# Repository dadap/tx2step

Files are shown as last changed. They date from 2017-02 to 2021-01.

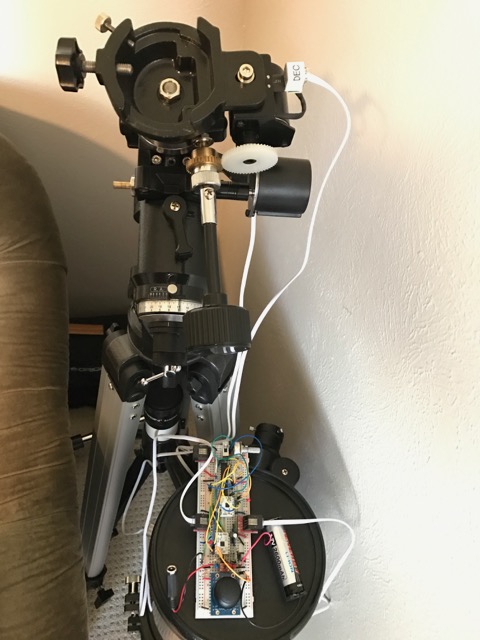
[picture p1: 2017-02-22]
img/tx2step-breadboard-proto.jpg

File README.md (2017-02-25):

Texas Two Step: A dual axis motor controller for equatorial telescope mounts
============================================================================

![Texas Two Step breadboard prototype controlling an unloaded Orion Astroview]
(https://github.com/dadap/tx2step/raw/master/img/tx2step-breadboard-proto.jpg)

Introduction
------------

The Texas Two Step is a replacement hand controller for the Synta Dual-Axis
motor kit for EQ-3 and EQ-5 type equatorial mounts (it can probably be adapted
to other mount designs utilizing stepper motors as well), with the following
improvements:

* Faster setting rates (original HC is limited to 8x sidereal)
* Analog 2-axis joystick to control setting rates (instead of rate slider switch
  combined with directional pad)
* ST-4 support with independent guiding (ST-4) and setting (joystick) rates.
* Main unit attaches to mount; RA, DEC, ST-4 cables move with telescope, and a
  single cable connects the control unit to a handheld joystick unit.
* Integrated rechargeable battery (to replace 4x D-cell pack, and eliminate the
  additional cable for power)
* All LEDs are dim and red to preserve dark adaptation
* Additional tracking rates (solar, lunar)
* Smaller and lighter
* Lower power draw (current prototype draws about .5 W for tracking)

The Texas Two Step is powered by an Atmel AVR microprocessor (currently an
Atmega328P on a breadboarded prototype circuit) and the stepper motors are
driven by dual TI DRV8834 low-voltage stepper driver ICs. The DRV8834 is
selected to allow a common power source (5V, boosted up from the output of a
single 18650 LiIon cell) for the logic and the motors.

TODO
----

A schematic and PCB layout should eventually be added to this repository.

The following features are not yet implemented:

* Directional switching not implemented; RA tracking direction is dependent on
  the order of stepper motor wiring to the driver boards. The final design is
  intended to allow switching between northern and southern hemisphere operation
  via a DIP switch or jumper setting.

The following features may or may not eventually be implemented:

* Backlash compensation (probably in the declination axis only; RA guiding at
  less than 1x tracking rate requires no backlash compensation.)
* Periodic error correction: implementing this will probably require some form
  of persistent storage, as the available EEPROM storage on the microcontroller
  is likely insufficient.

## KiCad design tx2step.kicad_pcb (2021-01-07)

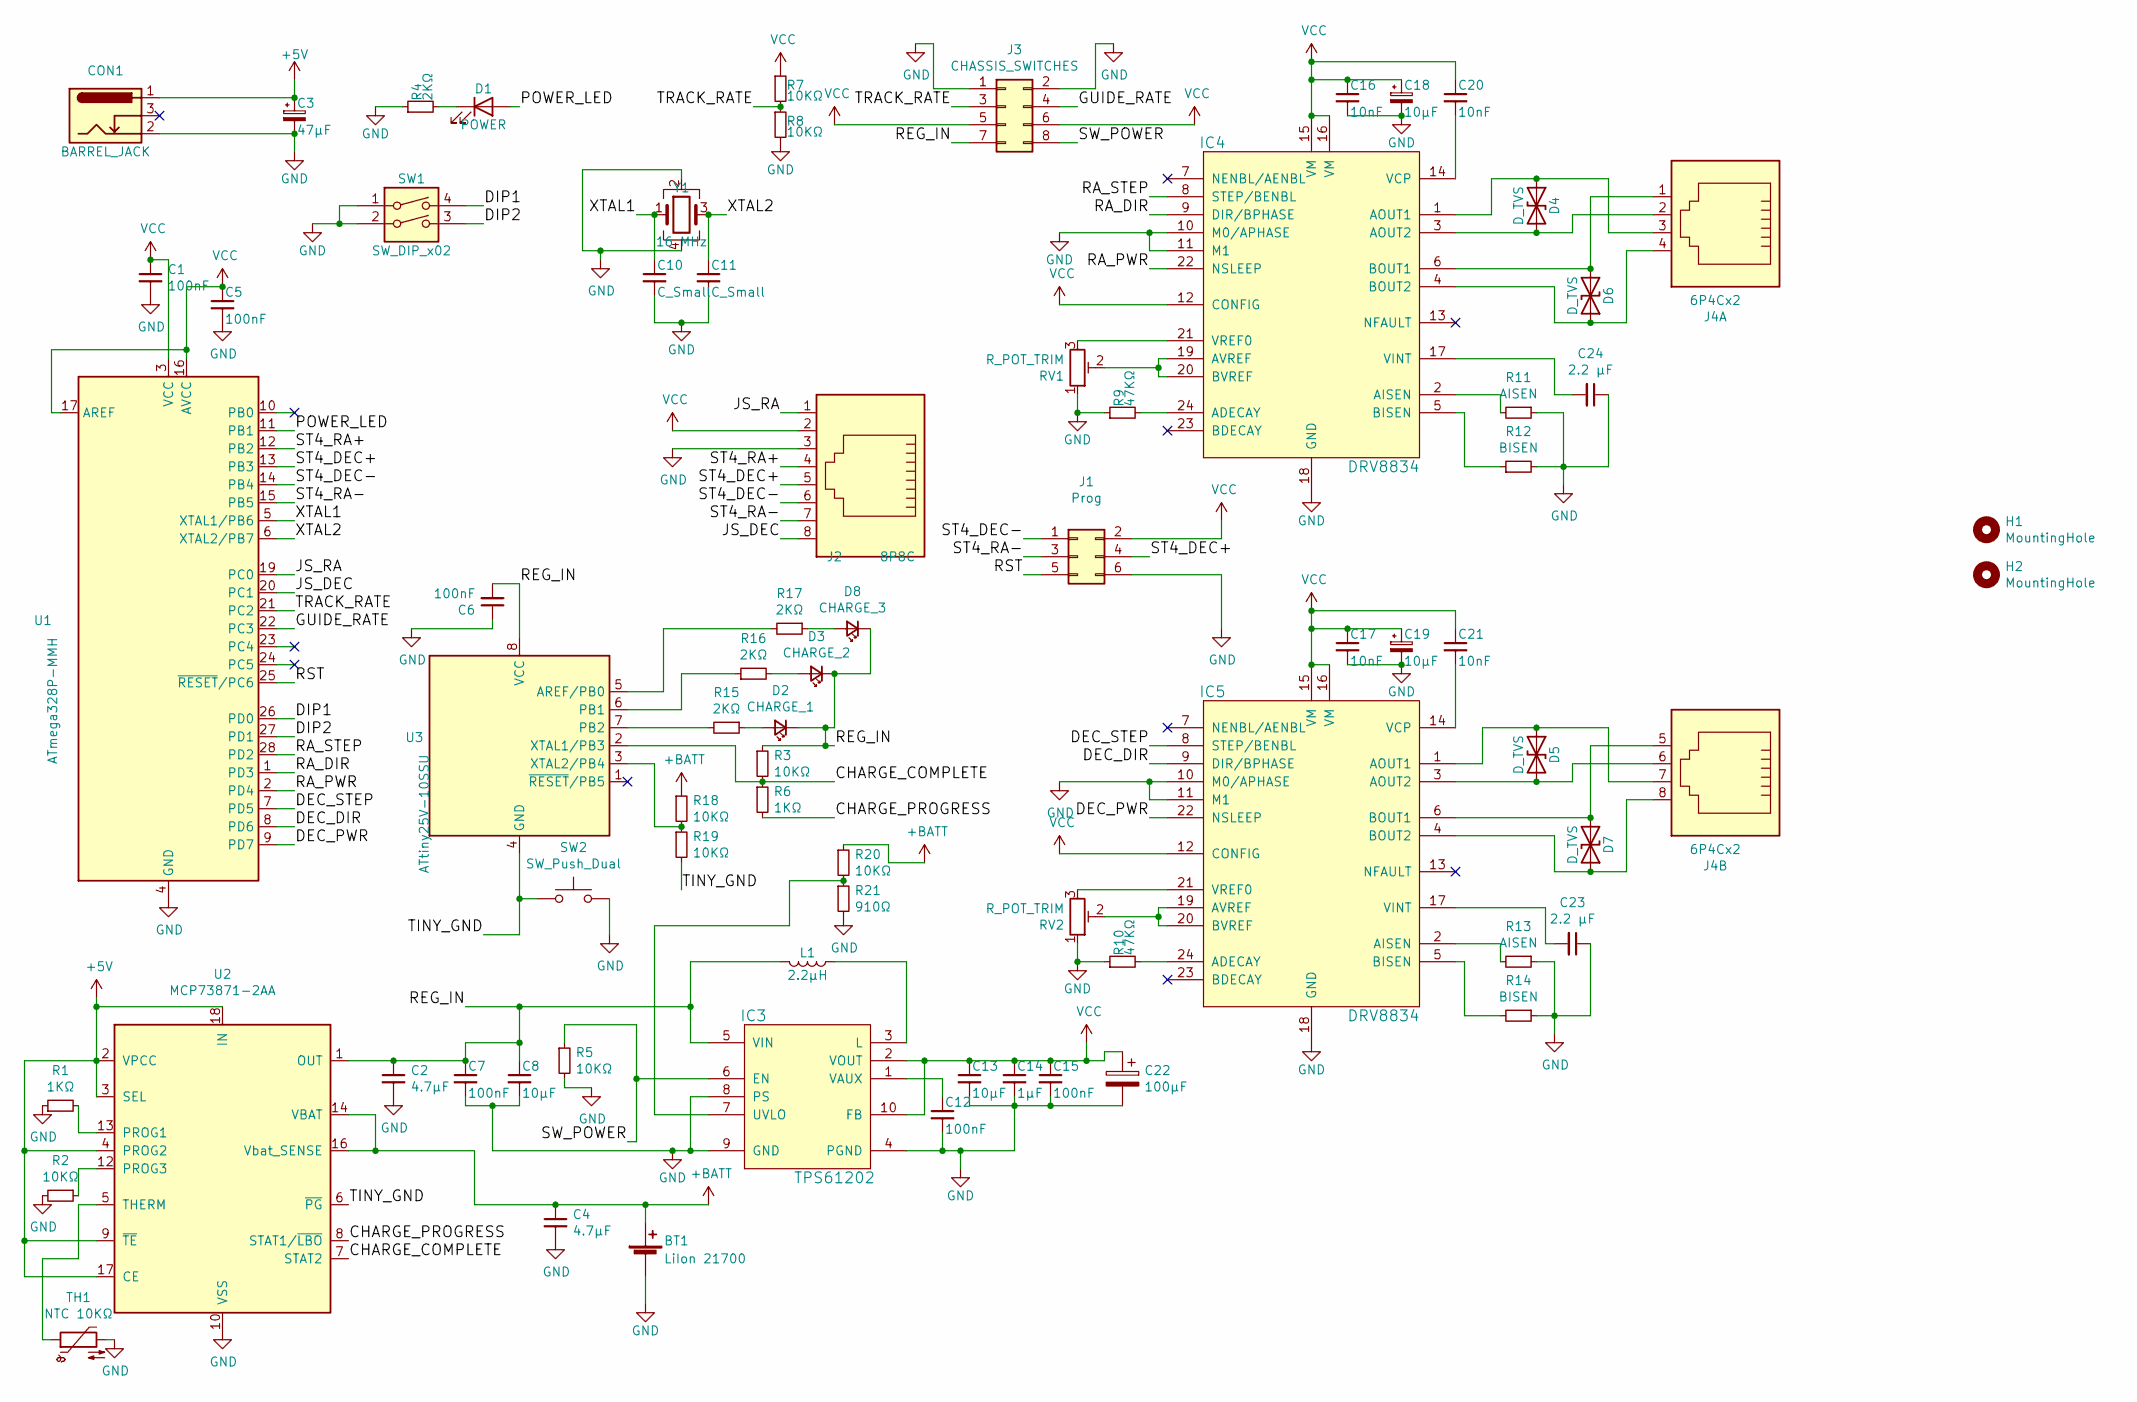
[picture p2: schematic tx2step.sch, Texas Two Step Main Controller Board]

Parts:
BT1: LiIon 21700; Battery_Clip_21700
C1, C5, C6, C7, C12, C15: 100nF; C_0603_1608Metric
C2, C4: 4.7µF; C_0603_1608Metric
C3: 47µF; CP_Radial_D5.0mm_P2.00mm
C8, C13, C18, C19: 10µF; C_0805_2012Metric
C10, C11: C_Small; C_0603_1608Metric
C14: 1µF; C_0603_1608Metric
C16, C17, C20, C21: 10nF; C_0603_1608Metric
C22: 100µF; CP_Radial_D5.0mm_P2.00mm
C23, C24: 2.2 µF; C_0603_1608Metric
CON1: BARREL_JACK; BarrelJack_Horizontal
D1: POWER; LED_0603_1608Metric
D2: CHARGE_1; LED_0603_1608Metric
D3: CHARGE_2; LED_0603_1608Metric
D4, D5, D6, D7: D_TVS; D_SOD-323
D8: CHARGE_3; LED_0603_1608Metric
H1, H2: MountingHole; MountingHole_3.2mm_M3
IC3: TPS61202; Texas_S-PVSON-N10_ThermalVias
IC4, IC5: DRV8834; QFN-24-1EP_4x4mm_P0.5mm_EP2.6x2.6mm_ThermalVias
J1: Prog; PinHeader_2x03_P2.54mm_Vertical
J2: 8P8C; RJ45_Amphenol_54602-x08_Horizontal
J3: CHASSIS_SWITCHES; PinHeader_2x04_P2.54mm_Vertical
J4: 6P4Cx2
L1: 2.2µH; L_1008_2520Metric
R1, R6: 1KΩ; R_0603_1608Metric
R2, R3, R5, R7, R8, R18, R19, R20: 10KΩ; R_0603_1608Metric
R4, R15, R16, R17: 2KΩ; R_0603_1608Metric
R9, R10: 47KΩ; R_0603_1608Metric
R11, R13: AISEN; R_0603_1608Metric
R12, R14: BISEN; R_0603_1608Metric
R21: 910Ω; R_0603_1608Metric
RV1, RV2: R_POT_TRIM; Potentiometer_Bourns_TC33X_Vertical
SW1: SW_DIP_x02; DIP-4_W7.62mm
SW2: SW_Push_Dual; SW_SPST_TL3305A
TH1: NTC 10KΩ; R_0402_1005Metric
U1: ATmega328P-MMH; QFN-28-1EP_4x4mm_P0.45mm_EP2.4x2.4mm
U2: MCP73871-2AA; QFN-20-1EP_4x4mm_P0.5mm_EP2.5x2.5mm
U3: ATtiny25V-10SSU; SOIC-8_3.9x4.9mm_P1.27mm
Y1: 16 MHz; Crystal_SMD_3225-4Pin_3.2x2.5mm

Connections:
+5V: C3.1, CON1.1, U2.2 (VPCC), U2.3 (SEL), U2.4 (PROG2), U2.9 (~TE), U2.17 (CE), U2.18 (IN), U2.19 (IN)
+BATT: BT1.1 (+), C4.1, R18.1, R20.1, U2.14 (VBAT), U2.15 (VBAT), U2.16 (Vbat_SENSE)
/CHARGE_COMPLETE: R3.2, R6.1, U2.7 (STAT2), U3.2 (XTAL1/PB3)
/CHARGE_PROGRESS: R6.2, U2.8 (STAT1/~LBO~)
/DEC_DIR: IC5.9 (DIR/BPHASE), U1.8 (PD6)
/DEC_PWR: IC5.22 (NSLEEP), U1.9 (PD7)
/DEC_STEP: IC5.8 (STEP/BENBL), U1.7 (PD5)
/DIP1: SW1.4, U1.26 (PD0)
/DIP2: SW1.3, U1.27 (PD1)
/GUIDE_RATE: J3.4, U1.22 (PC3)
/JS_DEC: J2.8, U1.20 (PC1)
/JS_RA: J2.1, U1.19 (PC0)
/POWER_LED: D1.2 (A), U1.11 (PB1)
/RA_DIR: IC4.9 (DIR/BPHASE), U1.1 (PD3)
/RA_PWR: IC4.22 (NSLEEP), U1.2 (PD4)
/RA_STEP: IC4.8 (STEP/BENBL), U1.28 (PD2)
/REG_IN: C2.1, C6.2, C7.1, C8.1, D2.1 (K), D3.1 (K), D8.1 (K), IC3.5 (VIN), J3.7, L1.2, R3.1, U2.1 (OUT), U2.20 (OUT), U3.8 (VCC)
/RST: J1.5, U1.25 (~RESET~/PC6)
/ST4_DEC+: J1.4, J2.5, U1.13 (PB3)
/ST4_DEC-: J1.1, J2.6, U1.14 (PB4)
/ST4_RA+: J2.4, U1.12 (PB2)
/ST4_RA-: J1.3, J2.7, U1.15 (PB5)
/SW_POWER: IC3.6 (EN), J3.8, R5.1
/TINY_GND: R19.2, SW2.1, U2.6 (~PG~), U3.4 (GND)
/TRACK_RATE: J3.3, R7.2, R8.1, U1.21 (PC2)
/XTAL1: C10.1, U1.5 (XTAL1/PB6), Y1.1
/XTAL2: C11.1, U1.6 (XTAL2/PB7), Y1.3
GND: BT1.2 (-), C1.2, C2.2, C3.2, C4.2, C5.2, C6.1, C7.2, C8.2, C10.2, C11.2, C12.2, C13.2, C14.2, C15.2, C16.2, C17.2, C18.2, C19.2, C22.2, C23.1, C24.1, CON1.2, IC3.4 (PGND), IC3.8 (PS), IC3.9 (GND), IC3.11 (GND), IC4.10 (M0/APHASE), IC4.11 (M1), IC4.18 (GND), IC4.25 (GND), IC5.10 (M0/APHASE), IC5.11 (M1), IC5.18 (GND), IC5.25 (GND), J1.6, J2.3, J3.1, J3.2, R1.1, R2.2, R4.1, R5.2, R8.2, R9.1, R10.1, R11.1, R12.2, R13.1, R14.1, R21.2, RV1.1, RV2.1, SW1.1, SW1.2, SW2.2, TH1.2, U1.4 (GND), U1.18 (GND), U1.29 (GND), U2.10 (VSS), U2.11 (VSS), U2.21 (VSS), Y1.2, Y1.4
unnamed: C12.1, IC3.1 (VAUX)
unnamed: C20.2, IC4.14 (VCP)
unnamed: C21.2, IC5.14 (VCP)
unnamed: C23.2, IC5.17 (VINT)
unnamed: C24.2, IC4.17 (VINT)
unnamed: D1.1 (K), R4.2
unnamed: D2.2 (A), R15.1
unnamed: D3.2 (A), R16.2
unnamed: D4.1 (A1), IC4.1 (AOUT1), J4.3
unnamed: D4.2 (A2), IC4.3 (AOUT2), J4.2
unnamed: D5.1 (A1), IC5.1 (AOUT1), J4.7
unnamed: D5.2 (A2), IC5.3 (AOUT2), J4.6
unnamed: D6.1 (A1), IC4.4 (BOUT2), J4.4
unnamed: D6.2 (A2), IC4.6 (BOUT1), J4.1
unnamed: D7.1 (A1), IC5.4 (BOUT2), J4.8
unnamed: D7.2 (A2), IC5.6 (BOUT1), J4.5
unnamed: D8.2 (A), R17.1
unnamed: IC3.3 (L), L1.1
unnamed: IC3.7 (UVLO), R20.2, R21.1
unnamed: IC4.2 (AISEN), R11.2
unnamed: IC4.5 (BISEN), R12.1
unnamed: IC4.19 (AVREF), IC4.20 (BVREF), RV1.2
unnamed: IC4.21 (VREF0), RV1.3
unnamed: IC4.24 (ADECAY), R9.2
unnamed: IC5.2 (AISEN), R13.2
unnamed: IC5.5 (BISEN), R14.2
unnamed: IC5.19 (AVREF), IC5.20 (BVREF), RV2.2
unnamed: IC5.21 (VREF0), RV2.3
unnamed: IC5.24 (ADECAY), R10.2
unnamed: R1.2, U2.13 (PROG1)
unnamed: R2.1, U2.12 (PROG3)
unnamed: R15.2, U3.7 (PB2)
unnamed: R16.1, U3.6 (PB1)
unnamed: R17.2, U3.5 (AREF/PB0)
unnamed: R18.2, R19.1, U3.3 (XTAL2/PB4)
unnamed: TH1.1, U2.5 (THERM)
VCC: C1.1, C5.1, C13.1, C14.1, C15.1, C16.1, C17.1, C18.1, C19.1, C20.1, C21.1, C22.1, IC3.2 (VOUT), IC3.10 (FB), IC4.12 (CONFIG), IC4.15 (VM), IC4.16 (VM), IC5.12 (CONFIG), IC5.15 (VM), IC5.16 (VM), J1.2, J2.2, J3.5, J3.6, R7.1, U1.3 (VCC), U1.16 (AVCC), U1.17 (AREF)

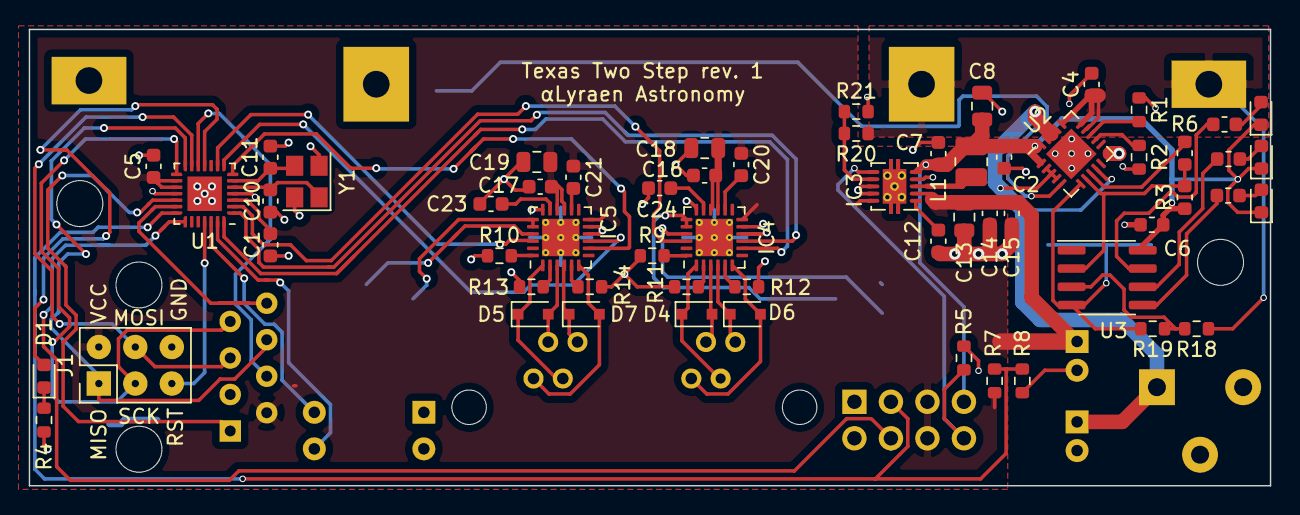
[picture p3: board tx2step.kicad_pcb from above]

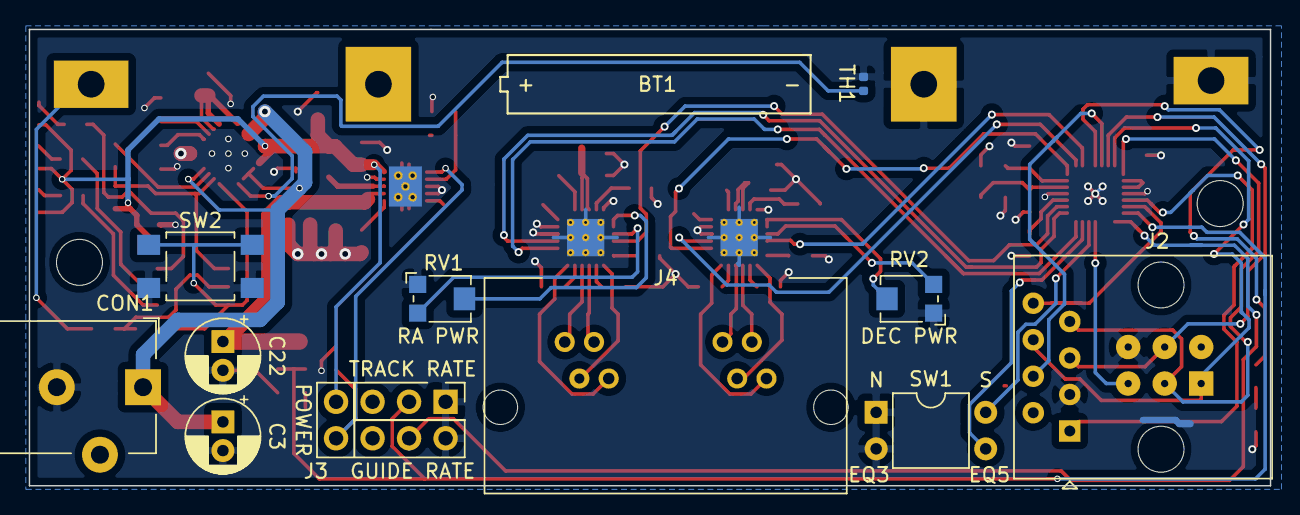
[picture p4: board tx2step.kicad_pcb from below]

Board: 2 copper layers, 86.4 x 31.8 mm, 73 parts (12 on the bottom side), 65 nets.

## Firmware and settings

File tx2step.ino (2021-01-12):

/*
 * Texas Two Step:
 *     A dual axis stepper motor controller for equatorial telescope mounts
 *
 * Copyright (c) 2017 Daniel Dadap
 *
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
 * THE SOFTWARE IS PROVIDED "AS IS", WITHOUT WARRANTY OF ANY KIND, EXPRESS OR
 * IMPLIED, INCLUDING BUT NOT LIMITED TO THE WARRANTIES OF MERCHANTABILITY,
 * FITNESS FOR A PARTICULAR PURPOSE AND NONINFRINGEMENT. IN NO EVENT SHALL THE
 * AUTHORS OR COPYRIGHT HOLDERS BE LIABLE FOR ANY CLAIM, DAMAGES OR OTHER
 * LIABILITY, WHETHER IN AN ACTION OF CONTRACT, TORT OR OTHERWISE, ARISING FROM,
 * OUT OF OR IN CONNECTION WITH THE SOFTWARE OR THE USE OR OTHER DEALINGS IN THE
 * SOFTWARE.
 */

#define DEBUG 0

#if (64 / clockCyclesPerMicrosecond()) * clockCyclesPerMicrosecond() != 64 || \
    F_CPU % 1000000L != 0
#error clockCyclesPerMicrosecond() does not divide evenly into 64: tracking \
rate may be inaccurate. Change this error into a warning if you wish to \
continue anyway.
#endif

typedef enum {
    RIGHT_ASCENSION = 0,
    DECLINATION = 1,
    NUM_AXES
} axis_index;

typedef enum {
    JOYSTICK_RA = RIGHT_ASCENSION,
    JOYSTICK_DEC = DECLINATION,
    TRACKING_RATE,
    GUIDING_RATE,
    CHARGER_STATUS,
    NUM_ANALOG_SENSORS
} analog_index;

typedef enum {
    NORMAL,
    IMMEDIATE,
    INITIAL,
} urgency;

typedef enum {
    TRISTATE_LOW = 0,
    TRISTATE_HI_Z = 1,
    TRISTATE_HIGH = 2,
} tristate_value;

typedef enum {
    LUNAR = TRISTATE_LOW,
    SOLAR = TRISTATE_HI_Z,
    SIDEREAL = TRISTATE_HIGH,
    NUM_TRACKING_RATES
} tracking_rate;

typedef enum {
    NEGATIVE,
    POSITIVE,
} direction;

/* Axis/motor attributes */
typedef struct {
    /* permanent configuration attributes */
    const unsigned long steps_per_15_degrees; /* steps per 15° (1 hour) */
    const int step_pin; /* pin to drive stepper pulses */
    const int dir_pin; /* pin to set motor direction */
    const int enable_pin; /* pin to enable/disable driver */

    /* dynamic runtime variables */
    unsigned long last_step; /* µsec timestamp of most recent step */
    unsigned long next_step; /* µsec timestamp of next scheduled step */
    int current_rate; /* tracking/setting rate in units of 1/4 tracking rate */
    unsigned long us_per_step; /* µs per step at current rate (cached value) */
} axis;

/* Analog sensor attributes */
typedef struct {
    /* permanent configuration attributes */
    const int pin; /* pin where value will be read */
    const int range_max; /* maximum value to map to */
    const bool affects_tracking; /* Whether sensor influences tracking rate */

    /* dynamic runtime variables */
    int mapped_value; /* storage for most recently read and mapped value */
} analog_sensor;

/* ST-4 configuration */
typedef struct {
    /* permanent configuration attributes */
    const int pin; /* pin where value will be read */
    const axis_index axis; /* axis driven by pin */
    const direction dir; /* direction to drive axis */

    /* dynamic runtime variables */
    unsigned long last_changed; /* milliscond timestamp of last value change */
    bool undebounced_value; /* pending state while debouncing */
    bool value; /* most recent debounced value */
} st4_input;

/* Microseconds per 15 degrees, used to calculate tracking rates.
 * The resulting calculations should lead to a tracking error on the order
 * of a second per day, which is in line with the error inherent to
 * reasonably priced clock crystals */
const unsigned long us_per_15_degrees[] = {
    [LUNAR] = 3726180003,
    [SOLAR] = 3600000000,
    [SIDEREAL] = 3590170483,
};

/* Configuration values for RA and DEC axes.
 * steps_per_15_degrees values are for Synta EQ-3 with dual-axis kit */
static axis axes[] = {
    [RIGHT_ASCENSION] = {
        .steps_per_15_degrees = 2 * 120 * 130,
        .step_pin = 2, .dir_pin = 3, .enable_pin = 4,
    },
    [DECLINATION] = {
         /* XXX this is actually wrong because it doesn't account for the
          * clutch, but that's sort of okay, because it moves really fast */
        .steps_per_15_degrees = 2 * 80 * 65,
        .step_pin = 5, .dir_pin = 6, .enable_pin = 7,
    },
};

/* ST-4 pin mappings */
static st4_input st4_inputs[] = {
    { .pin = 10, .axis = RIGHT_ASCENSION, .dir = POSITIVE, },
    { .pin = 11, .axis = DECLINATION, .dir = POSITIVE, },
    { .pin = 12, .axis = DECLINATION, .dir = NEGATIVE, },
    { .pin = 13, .axis = RIGHT_ASCENSION, .dir = NEGATIVE, },
};

/* Table of setting rates, in units of 1/4 tracking rate, e.g.,
 * a rate value of "12" represents 3x tracking rate. */
const int setting_rates[] = {-160, -80, -40, -12, -4, -2, -1,
                             0, 0, 1, 2, 4, 12, 40, 80, 160};

/* Table of guiding rates, in same units as setting rates. Duplicated values
 * for rates < 1x tracking are to ensure that 1x tracking is at the midpoint. */
const int guiding_rates[] = {1, 1, 2, 2, 3, 3, 4, 6, 8, 12, 32, 64, 128};

#define array_len(a) (sizeof(a) / sizeof(a[0]))

/* Configuration values for analog inputs */
static analog_sensor sensors[] = {
    [JOYSTICK_RA] = {
        .pin = A0, .range_max = array_len(setting_rates),
        .affects_tracking = true,
    },
    [JOYSTICK_DEC] = {
        .pin = A1, .range_max = array_len(setting_rates),
        .affects_tracking = true,
    },
    [TRACKING_RATE] = {
        .pin = A2, .range_max = NUM_TRACKING_RATES,
        .affects_tracking = true,
    },
    [GUIDING_RATE] = {
        .pin = A3, .range_max = array_len(guiding_rates),
        .affects_tracking = false,
    },
};

const int led_pwm_pin = 9;

/* Determine whether a step is due (current time is the same as or after next
 * due step). last_step is used as a reference point to handle overflow. */
static inline bool step_due(axis_index i, unsigned long now)
{
    return now - axes[i].last_step >= axes[i].next_step - axes[i].last_step;
}

/* Perform a step on axis i if one is needed. */
static void do_step(axis_index i, urgency when)
{
    /* DRV8834 requires a 1.9 µs minimum pulse duration;
     * delayMicroseconds() is not precise < 3 µs according to docs */
    const int PULSE_DURATION_US = 4;

    /* Ignore next_step and avoid delay if the rate is 0 */
    if (axes[i].current_rate != 0) {
        unsigned long now = micros();

        /* Always step if when is IMMEDIATE, ignoring when next step is due */
        if (when == IMMEDIATE || when == INITIAL || step_due(i, now)) {
            /* Don't actually step if we're just initializing, but do reset
             * the last_step timestamp. */
            if (when != INITIAL) {
                digitalWrite(axes[i].step_pin, HIGH);
                delayMicroseconds(PULSE_DURATION_US);
                digitalWrite(axes[i].step_pin, LOW);
                delayMicroseconds(PULSE_DURATION_US);
            }

            axes[i].last_step = now;

            /* Reset next_step based on current time for IMMEDIATE steps or
             * when initializing; increment next_step by us_per_step for NORMAL
             * steps to allow for catching up to any missed steps. Don't bother
             * trying to catch up to missed steps when step rate > 50Hz, the
             * precision of step timing isn't critical at these speeds */
            if (when == IMMEDIATE || when == INITIAL ||
                axes[i].us_per_step < 20000) {
                axes[i].next_step = now + axes[i].us_per_step;
            } else {
                axes[i].next_step += axes[i].us_per_step;
            }
        }
    }
}

/* Calculate microseconds per step at given rate */
static inline unsigned long us_per_step(axis_index i, int rate)
{
    /* rate is given in units of 1/4 tracking rate and may be negative;
     * number of microseconds needs to be a scalar value. */
    return ((us_per_15_degrees[sensors[TRACKING_RATE].mapped_value] /
             axes[i].steps_per_15_degrees) * 4) / abs(rate);
}

/* Set the tracking, setting, or guiding rate on the given axis. Rates are
 * expressed in units of 1/4 the tracking rate. */
static void set_rate(axis_index i, int new_rate, urgency when)
{
    /* RA always tracks at +1x relative to nominal rate */
    if (i == RIGHT_ASCENSION) {
        new_rate += 4;
    }

    if (axes[i].current_rate != new_rate) {
        axes[i].current_rate = new_rate;

        /* Set direction (FIXME read direction toggle switch */
        if (new_rate < 0) {
            digitalWrite(axes[i].dir_pin, LOW);
        } else {
            digitalWrite(axes[i].dir_pin, HIGH);
        }

        /* Enable/disable motor and cache us_per_step value */
        if (new_rate != 0) {
            digitalWrite(axes[i].enable_pin, HIGH);
            delay(1); /* DRV8834 needs 1ms delay on wake before step */
            axes[i].us_per_step = us_per_step(i, new_rate);
        } else {
                digitalWrite(axes[i].enable_pin, LOW);
        }

        /* Step immediately and override next scheduled step,
         * unless we are just initializing a sensor. */
        do_step(i, when == INITIAL ? INITIAL : IMMEDIATE);
    }
}

/* Set rates based on the updated value of an analog sensor */
static void analog_set_rates(analog_index sensor, urgency when)
{
    int new_value = map(analogRead(sensors[sensor].pin),
                        0, 1024, 0, sensors[sensor].range_max);

    if (when == IMMEDIATE || when == INITIAL ||
        new_value != sensors[sensor].mapped_value) {
        sensors[sensor].mapped_value = new_value;

        if (sensors[sensor].affects_tracking) {
            for (int i = 0; i < NUM_AXES; i++) {
                set_rate(i, setting_rates[sensors[i].mapped_value], when);
            }
        }

#if DEBUG
        Serial.print("Sensor: ");
        Serial.print(sensor);
        Serial.print(" New value: ");
        Serial.print(new_value);
        Serial.print(" RA us/step: ");
        Serial.print(axes[RIGHT_ASCENSION].current_rate ?
                         axes[RIGHT_ASCENSION].us_per_step : 0);
        Serial.print(" DEC us/step: ");
        Serial.println(axes[DECLINATION].current_rate ?
                         axes[DECLINATION].us_per_step : 0);
#endif
    }
}

/* Calculate the effective rate driven by an ST-4 input, scaled by the value of
 * the guiding rate potentiometer. */
static int scale_st4_rate(int st4_index)
{
    int rate = guiding_rates[sensors[GUIDING_RATE].mapped_value];

    if (st4_inputs[st4_index].dir == NEGATIVE) {
        rate *= -1;
    }

    return rate;
}

/* Set guiding rates based on ST-4 input. Simultaneous inputs in opposing
 * directions on the same axis will cancel each other out. */
static void st4_set_rates(void)
{
    int net_rates[NUM_AXES];

    memset(net_rates, 0, sizeof(int) * NUM_AXES);

    for (int i = 0; i < array_len(st4_inputs); i++) {
        if (st4_inputs[i].value == true) {
            net_rates[st4_inputs[i].axis] += scale_st4_rate(i);
        }
    }

    for (int i = 0; i < NUM_AXES; i++) {
        set_rate(i, net_rates[i], NORMAL);
    }
}

/* Atmega328 ADC requires a minimum of 100µs between analog reads; we don't
 * need quite that level of resolution, but we should still try to rate limit
 * the reads somewhat */
const int ANALOG_READ_DELAY_MS = 10;
const int MIN_ANALOG_READ_DELAY_US = 100;

/* Read sensor values and adjust tracking/setting rates accordingly.
 * Don't perform an analog read unless sufficient time has elapsed since the
 * last read, or an immediate read was requested. Interleave reads between the
 * sensors. The actual reading is performed in set_rates(); this function serves
 * to enforce timing and interleaving. */
static void read_analog_sensor(urgency when)
{
    static analog_index next_read = JOYSTICK_RA;
    static unsigned long last_read_ms;
    unsigned long now = millis();

    if (when == INITIAL) {
        pinMode(sensors[next_read].pin, INPUT);
    }

    /* Wait minimum delay before an immediate read or when initializing */
    if (when == IMMEDIATE || when == INITIAL) {
        delayMicroseconds(MIN_ANALOG_READ_DELAY_US);
    }

    if (when == IMMEDIATE || now - last_read_ms >= ANALOG_READ_DELAY_MS) {
        last_read_ms = now;
        analog_set_rates(next_read, when);
        next_read = (next_read + 1) % NUM_ANALOG_SENSORS;
    }
}

/* Debounce ST-4 input. This may not be necessary for actual ST-4 guiders, but
 * digital hand control interfaces over ST-4, and may need switch debouncing. */
static void debounce_input(void)
{
    const int debounce_delay_ms = 20;

    for (int i = 0; i < array_len(st4_inputs); i++) {
        unsigned long now = millis();
        /* ST-4 input pins are pulled up high and short to ground when active */
        bool current_value = (digitalRead(st4_inputs[i].pin) == LOW);

        if (current_value != st4_inputs[i].undebounced_value) {
            st4_inputs[i].last_changed = now;
            st4_inputs[i].undebounced_value = current_value;
            continue;
        }

        if (now - st4_inputs[i].last_changed >= debounce_delay_ms &&
            st4_inputs[i].value != st4_inputs[i].undebounced_value) {
            st4_inputs[i].value = st4_inputs[i].undebounced_value;
#if DEBUG
            Serial.print("ST4 pin ");
            Serial.print(i);
            Serial.print(": ");
            Serial.println(st4_inputs[i].value);
#endif
        }
    }
}

/* Returns true if the joystick is in a neutral position. */
static bool joystick_neutral(void)
{
    bool ret = true;

    for (int i = 0; i < NUM_AXES; i++) {
        ret &= (setting_rates[sensors[i].mapped_value] == 0);
    }

    return ret;
}

/* Set the status LED based on activity:
 *   - Solid LED when tracking
 *   - Blinking LED when setting
 */
static void update_led(urgency when)
{
    const int cycle_duration = 2048;
    unsigned long now = millis() % cycle_duration;
    static int led_value;
    int new_led_value;

    if (joystick_neutral()) {
            new_led_value = 160;
    } else {
        if (now < cycle_duration / 2) {
            new_led_value = 255;
        } else {
                new_led_value = 0;
        }
    }

    if (when == INITIAL || new_led_value != led_value) {
        led_value = new_led_value;
        analogWrite(led_pwm_pin, led_value);
    }
}

void setup()
{
#if DEBUG
    Serial.begin(9600);
#endif
    for (int i = 0; i < NUM_AXES; i++) {
        pinMode(axes[i].step_pin, OUTPUT);
        pinMode(axes[i].dir_pin, OUTPUT);
        pinMode(axes[i].enable_pin, OUTPUT);
    }

    for (int i = 0; i < NUM_ANALOG_SENSORS; i++) {
        read_analog_sensor(INITIAL);
    }

    for (int i = 0; i < array_len(st4_inputs); i++) {
        pinMode(st4_inputs[i].pin, INPUT_PULLUP);
    }

    pinMode(led_pwm_pin, OUTPUT);
    update_led(INITIAL);
}

void loop()
{
    read_analog_sensor(NORMAL);
    debounce_input();

    /* Joystick input overrides ST-4 input. */
    if (joystick_neutral()) {
        st4_set_rates();
    }

    for (int i = 0; i < NUM_AXES; i++) {
        do_step(i, NORMAL);
    }

    update_led(NORMAL);
}

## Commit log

2017-02-04 Microcontroller code for Texas Two Step, initial commit
    The Texas Two Step is a replacement hand controller for the Synta
    Dual-Axis motor kit for EQ-3 and EQ-5 type equatorial mounts, with
    the following improvements:
    * Faster setting rates (original HC is limited to 8x sidereal)
    * Analog 2-axis joystick to control setting rates (instead of
    rate slider switch combined with directional pad)
    * ST-4 support with independent guiding (ST-4) and setting
    (joystick) rates.
    * Main unit attaches to mount; RA, DEC, ST-4 cables move with
    telescope, and a single cable connects the control unit to
    a handheld joystick unit.
    * Integrated rechargeable battery (to replace 4x D-cell pack,
    and elimina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
    [tx2step.ino]
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2017-02-04 Reduce interval between analog reads
    The ADC (bonus fix: correct comment with s/DAC/ADC/) requires a delay
    of 100 *micro*seconds between reads, not 100 *milli*seconds. Polling
    the joystick every 100 microseconds seems somewhat excessive, so drop
    the polling delay from 100ms to 20ms.
    [tx2step.ino]
2017-02-04 Remove 4µs magic number
    Replace the number "4" with a symbolic constant
    [tx2step.ino]
2017-02-04 Increase maximum setting speed to 32x
    Testing has demonstrated that RA setting speed can go to 32x before
    stalling: DEC can go a bit faster before stalling out due to gearing,
    but is already going faster because the steps_per_15_degrees value
    fails to take into account the spur gears for the clutch on the DEC
    axis. Expand the range of setting speeds to allow +/- 32x on RA.
    [tx2step.ino]
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2017-02-04 Mark all helper functions as static
    Add the static keyword to the signatures of all helper functions, to
    allow the compiler to choose optimized calling conventions, etc.,
    since these functions won't need to be accessed from other translation
    units. Also add the inline keyword to the more trivial helpers, though
    the compiler will have probably decided to inline them anyway.
    [tx2step.ino]
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2017-02-17 Reassign stepper driver control pins
    Pins 11 through 13 will soon be reassigned to the ST-4 port, to allow the
    ST-4 port to serve double duty as an ISP port for reprogramming the MCU.
    The RA axis is assigned an enable pin again, to support enforcing a delay
    between power on and stepping.
    This sketch is no longer compatible with the Adafruit Pro Trinket, due to
    use of pins that are unavailable on that board. (The recent change to
    validate the clock rate already made this sketch incompatible with the
    3V version of the Pro Trinket, which is clocked at 12 MHz.)
    [tx2step.ino]
2017-02-17 Wait 1ms after enabling motor
    The DRV8834 datasheet specifies a 1ms minimum time between waking up the
    driver and stepping. The RA axis currently intermittently does not work,
    but can be recovered by unplugging the jumper from the enable pin on the
    driver board to Vcc and plugging it back in again; add a 1ms delay after
    enabling the driver in case the missing delay is responsible for this
    intermittent failure.
    [tx2step.ino]
2017-02-21 Add support for multiple setting rates
    Assign an additional analog pin to read a switch (SPDT on-off-on, read
    common pin which is tied to a pair of voltage dividing resistors) to
    set the tracking rate. Since the number of analog reads is no longer
    the same as the number of axes, refactor the joystick reading code to
    be more generic analog reading code and decouple it from the axes.
    The us_per_15_degrees values are based upon a sidereal day of 23h 56m
    4.0916s and a sidereal month of 27d 7h 43m 11.5s, both figures obtained
    from the Wikipedia articles for "Sidereal time" and "Lunar month",
    respectively.
    [tx2step.ino]
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2017-02-21 Add sensor for ST-4 guiding rate
    A potentiometer will eventually set the guiding rate for corrections
    coming over the ST-4 interface. Assign a pin to read this potentiometer
    but don't actually do anything besides store its mapped value. (i.e.,
    this will have no effect until ST-4 support is added.)
    Also increase the sensor polling rate, now that there are twice as
    many sensors as there were originally.
    [tx2step.ino]
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2017-02-21 Fix comments regarding tracking rates
    The tracking rate is no longer fixed to sidereal time, so adjust all
    comments referring to sidereal time to be more generic. Also correct
    inverted units to 4x instead of 1/4.
    [tx2step.ino]
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2017-02-22 Fix rate units in comments
    Partially revert commit 49c4de7cf976f975a3846f1d6528e56ce28cea5f, which
    incorrectly "corrected" the 1/4 to 4x in comments describing the units
    that tracking/setting/guiding rates are expressed in. 1/4 is correct,
    as one *unit* represents 25% of the tracking rate.
    [tx2step.ino]
2017-02-22 Don't bother catching up on missed steps at high speeds
    Catching up on missed steps mostly makes sense when attempting to track
    precisely at a fixed rate. The precision is less important when setting
    or guiding, and missed steps are more likely at higher speeds, so don't
    bother trying to catch up on missed steps when stepping faster than 50
    steps per second to hopefully smooth out stuttering at high speeds.
    [tx2step.ino]
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2017-02-24 Remove short_name field from axis struct
    This isn't used any more by the current debug print code.
    [tx2step.ino]
2017-02-25 Add support for ST-4 guiding
    Assign pins 10 through 13 for ST-4, and add code to debounce ST-4
    input and adjust the rate based on the combination of ST-4 input and
    the guiding rate set by the GUIDING_RATE potentiometer. Pins 10 through
    13 are selected because pins 11 through 13 are used for SPI; pin ST-4
    pin 3 will be connected to pin 10 when the controller is on, and to
    RESET when the controller is off, to allow for reprogramming the
    microcontroller over the ST-4 port.
    [tx2step.ino]
2017-02-28 Initial WIP schematic
    Add a partial Kicad schematic for the Texas Two Step. For now, only the
    three main ICs (Atmega328P, 2x DRV8834) and a handful of supporting
    components are present.
    [tx2step.sch]
2017-02-28 Resize schematic to US Letter
    [tx2step.sch]
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2017-03-01 Remove pullup resistor on RESET
    There won't be a physical reset button, and ISP seems to work fine
    without the pullup.
    [tx2step.sch]
2017-03-01 Create separate logic supply
    The main microcontroller IC may be powered directly from the DC barrel
    jack when power to the rest of the system is shut down. AREF is left
    connected to the main voltage rail.
    [tx2step.sch]
2017-03-01 Share bypass capacitor for VCC and AVCC
    [tx2step.sch]
2017-03-02 Use separate logic power rail for analog reference
    Connect the V+ pin on the enhanced ST-4 connector to +5VL (the
    dedicated logic power supply) rather than VCC, so that the logic
    voltage is used as the reference voltage for analog sensors such as
    the joystick potentiometers.
    Wire up power to the DRV8834 ICs as well.
    [tx2step.sch]
2017-03-02 Fix errors in DRV8834 component
    Add missing pins, remap misnumbered pins
    [tx2step.sch]
2017-03-02 Rename drv8834.lib to tx2step.lib
    There will be a number of other components used in this project which
    are not currently in any of the kicad libraries; rename the drv8834
    library to reflect the project name, so that all of the custom
    components can share a single library.
    [tx2step.sch]
2017-03-02 Add MCP73831
    Add MCP73831 (battery charging IC) component, leave it disconnected
    for now.
    [tx2step.sch]
2017-03-02 Move DRV8834 label to corner
    [tx2step.sch]
2017-03-02 Add rate selector switches
    [tx2step.sch]
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2017-03-02 Fully wire up DRV8834 chips
    The selection of external supporting components is based in part on
    the example application circuit in the DRV8834 datasheet, and in part
    on the design of the Pololu DRV8834 breakout board.
    The voltage divider and current sense resistor values listed in the
    schematic should program a current limit of 117mA per phase, which is
    in line with the current limit selected by the potentiometers in the
    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
    [tx2step.sch]
2017-03-02 Add additional power ICs
    TPS2113A power multiplexer and TPS61202 boost converter.
    Not wired up yet.
    [tx2step.sch]
2017-03-02 Connect MCP73831 and battery
    [tx2step.sch]
2017-03-02 Connect DC in and battery to multiplexer
    The DC in source will take priority. Also connect the charge state LED.
    [tx2step.sch]
2017-03-02 Separate DC power from power area of schematic
    This makes it a little cleaner and easier to visualize the relationship
    between the DC in source and the logic/main voltage rails.
    [tx2step.sch]
2017-03-02 Wire up TPS61202 boost regulator and power side of DPDT switch
    The power supply circuit should now be complete.
    [tx2step.sch]
2017-03-02 Add DIP switch for settings
    All of the pins on the MCU are now occupied!
    [tx2step.sch]
2017-03-02 Place NC flags on pins intentionally left unconnected
    [tx2step.sch]
2017-03-02 Add project info to schematic
    [tx2step.sch]
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2017-03-02 Connect error LEDs to DRV8834s
    Also give the other two LEDs names
    [tx2step.sch]
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2017-03-02 Add NC flags to all remaining unconnected pins
    Also fix broken connection to a capacitor
    [tx2step.sch]
2020-10-27 Remap symbols to new format
    [tx2step.sch]
2020-10-27 Delete +5VL net
    Simplify power supply since the TPS2113A auto-muxes the DC input
    anyway and just power logic directly from the regulator. Also
    avoids running logic off unregulated DC input.
    [tx2step.sch]
2020-10-27 Fix barrel jack connection
    GND was connected to wrong barrel jack pin. Connect to both the
    sleeve (pin 2) and the switch (pin 3) as we don't actually use
    the switch functionality.
    [tx2step.sch]
2020-10-27 Use unshielded jacks
    Reduces number of NC pins
    [tx2step.sch]
2020-10-27 Remove debug mode switch
    Add an edge connector debug interface rather than overloading the
    remote connector for reprogramming.
    [tx2step.sch]
2020-10-27 Simplify DRV8834 current limit configuration
    Wire A/B VREF directly to VREFO and connect the ISEN pins to a
    resistor network. The current limiting can be adjusted by swapping
    the resistor value.
    [tx2step.sch]
2020-10-27 Use DC jack switch for LED
    Repurpose power LED for use as a "running on battery" indicator.
    If the unit is running while plugged in, the charge indicator will
    indicate power.
    [tx2step.sch]
2020-10-28 Use labeled nets
    Clean up the schematic by using labeled nets between the ucontroller
    and other components. Also remove the pin to the power switch, as
    the microcontroller is no longer powered when the power switch is
    off, and reuse it to detect whether the DC connector is plugged in.
    [tx2step.sch]
2020-10-28 Use SPST for power switch
    Add pullup resistor, unit is powered on when switch is open; off
    when closed.
    [tx2step.sch]
2020-10-28 Replace switches with pin header
    This allows the switches to be mounted on the chassis, freeing up
    space on the board and allowing for component flexibility.
    [tx2step.sch]
2020-10-28 Delete rescue lib
    Remap all symbols to proper libraries
    [tx2step.sch]
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2020-11-03 Use multi-part component for combined 6P4C jack
    [tx2step.sch]
2020-11-08 Update footprints from BOM
    [tx2step.sch]
2020-11-08 Use regular 6-pin ISP for reprogramming
    Eliminate special edge connector that also exposes ST-4.
    [tx2step.sch]
2020-11-08 Add separate bypass capacitors for AVR VCC/AVCC
    They're on opposite sides of the chip and should probably each
    have their own bypass
    [tx2step.sch]
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2020-11-17 Use trimpots to adjust current clamping
    It turns out resistor networks aren't available in a wide variety of
    values. Replace the resistor network with fixed value resistors and
    add trimpots for each axis to adjust the current clamping.
    [tx2step.kicad_pcb, tx2step.sch]
2020-11-18 Fix up silkscreen collisions
    [tx2step.kicad_pcb]
2020-11-18 Add more power planes
    [tx2step.kicad_pcb]
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2020-11-18 Update silkscreen revision ID
    [tx2step.kicad_pcb]
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2020-11-21 more rerouting and cleanup
    [tx2step.kicad_pcb]
2020-11-24 Improve DRV8845 xISEN resistor courtyard clearances; fully connect thermal pads
    [tx2step.kicad_pcb]
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2021-01-01 move silkscreen to avoid collision
    [tx2step.kicad_pcb]
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2021-01-01 isp pads pogo only
    No need to access these pads from the other side, where they're
    covered by the 8P8C connector, which doesn't leave room for
    soldering through-hole headers.
    [tx2step.kicad_pcb]
2021-01-01 Fix AVR bypass capacitor values
    [tx2step.sch]
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2021-01-01 Restore capacitors on DRV8834 VINT
    This pin still needs a capacitor even if it's not being used to
    supply the CONFIG pin.
    [tx2step.kicad_pcb, tx2step.sch]
2021-01-01 Delete driver error LEDs
    They don't actually seem particularly useful
    [tx2step.kicad_pcb, tx2step.sch]
2021-01-01 fix minor clearance issues
    [tx2step.kicad_pcb]
2021-01-03 Replace MCP73831 and TPS2113A with MCP73871
    [tx2step.kicad_pcb, tx2step.sch]
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2021-01-05 Reverse trimpot pins
    Make clockwise increase the ILIM voltage
    [tx2step.kicad_pcb, tx2step.sch]
2021-01-07 Use FRE E5564 footprint for dual 6P4C
    Less expensive part than the Molex, and leaves more room to lay out
    the TVS diodes and ISEN resistors more nicely.
    [tx2step.kicad_pcb, tx2step.sch]
2021-01-07 Use mega328-driven LED for non-charge status
    Now that we have a separate uC for the charge progress/status LEDs,
    repurpose the existing LED to indicate controller reacting to input.
    [tx2step.sch]

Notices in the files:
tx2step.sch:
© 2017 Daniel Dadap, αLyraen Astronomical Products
